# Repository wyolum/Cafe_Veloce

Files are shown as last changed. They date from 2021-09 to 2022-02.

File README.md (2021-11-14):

# Cafe_Veloce
Controller board for eBicycle lighting
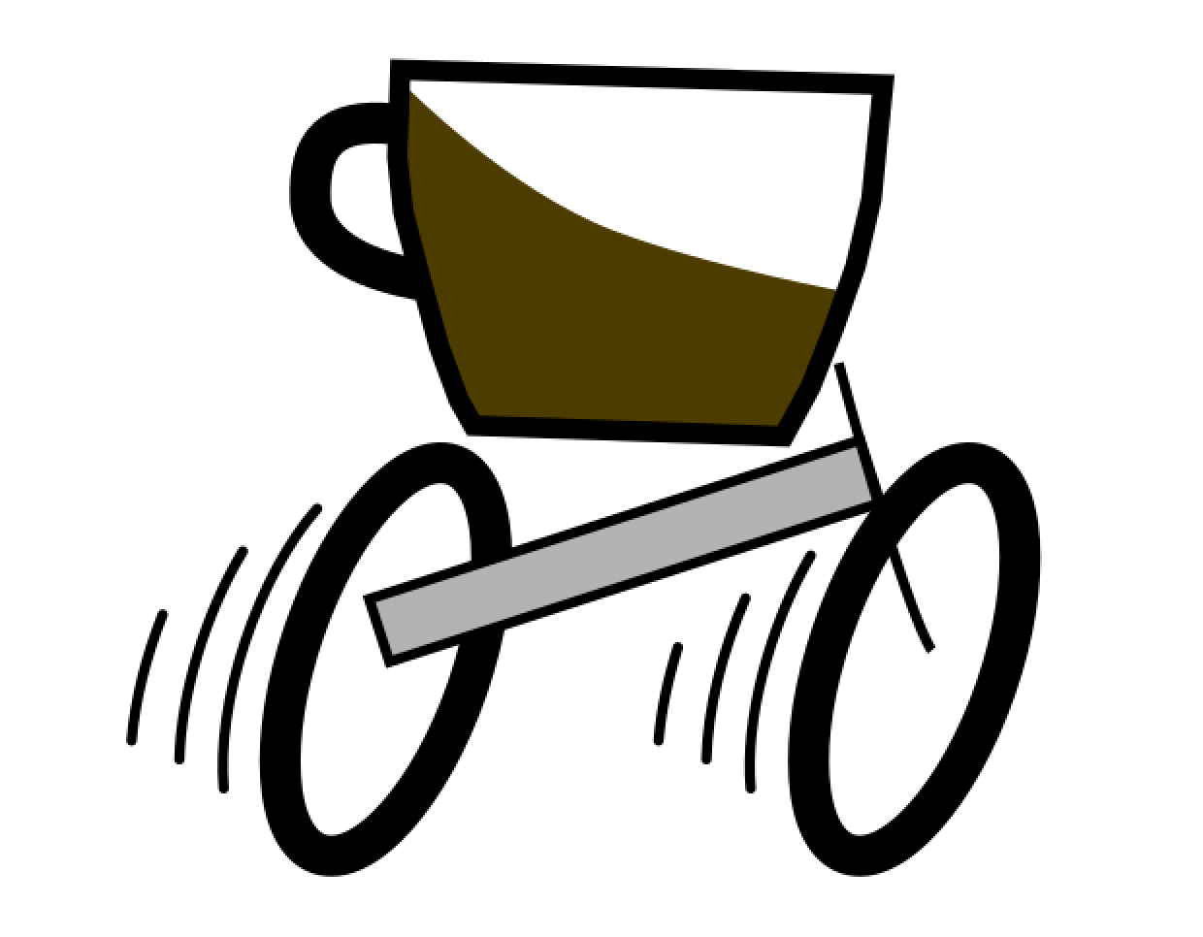
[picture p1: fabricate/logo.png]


**Renders**
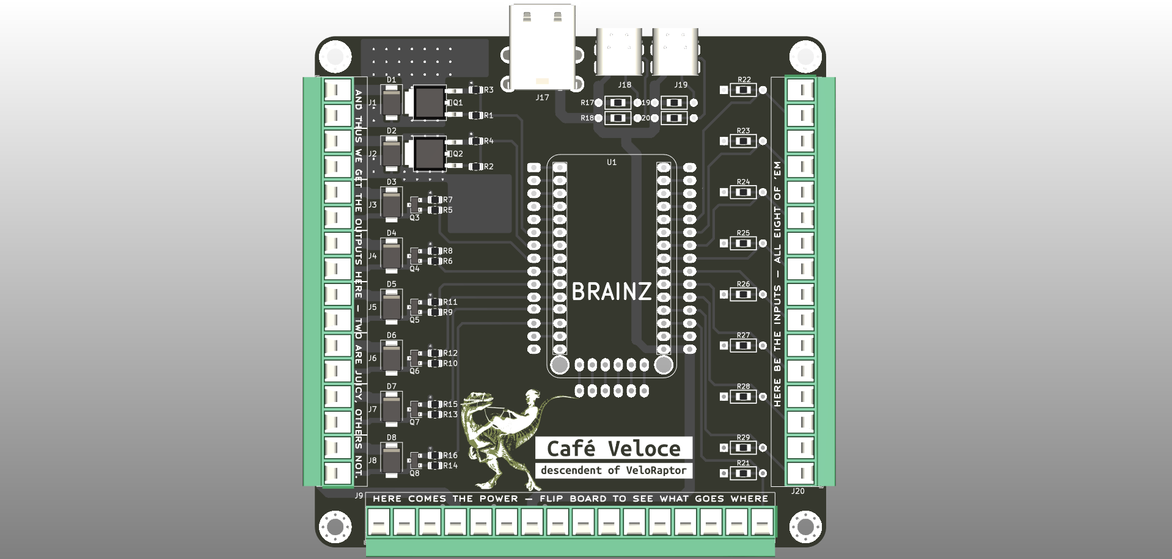
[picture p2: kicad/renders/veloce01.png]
Cafe Veloce


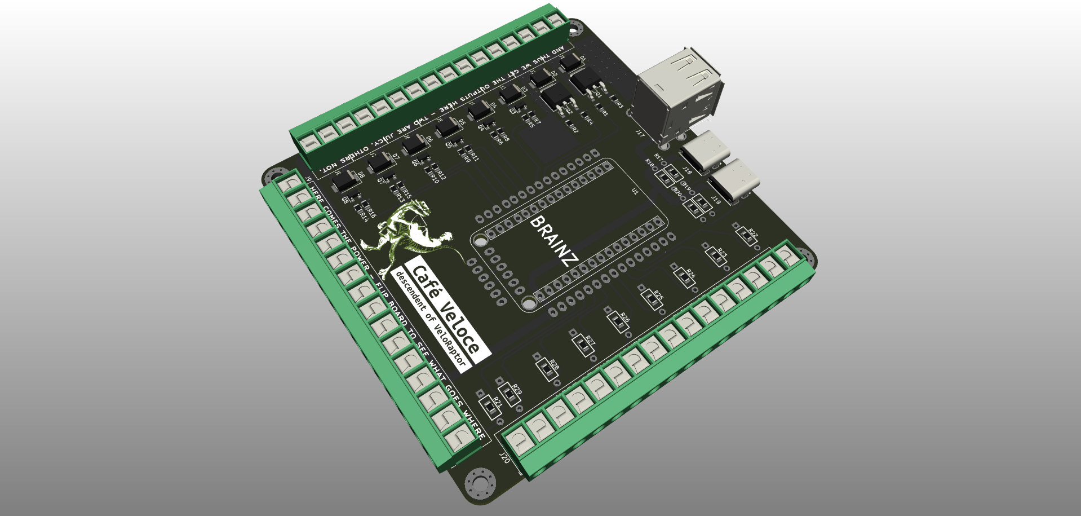
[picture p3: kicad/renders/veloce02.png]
Cafe Veloce


License
-------
[CERN Open Hardware Licence v1.2 ]

[CERN Open Hardware Licence v1.2 ]:http://www.ohwr.org/attachments/2388/cern_ohl_v_1_2.txt

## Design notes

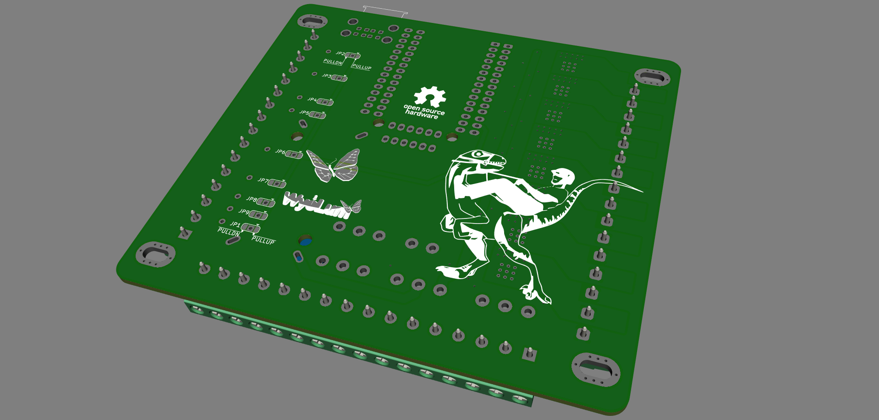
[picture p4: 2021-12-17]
kicad_v2/renders/veloce04.png

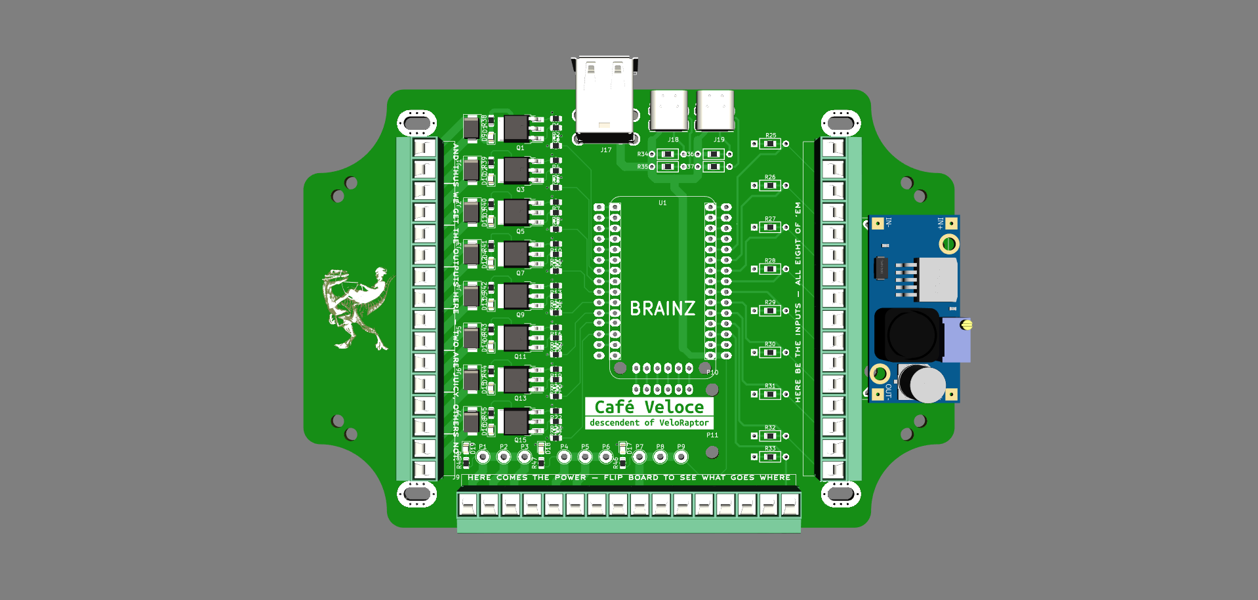
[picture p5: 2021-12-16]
kicad_v2/renders/veloce08.png

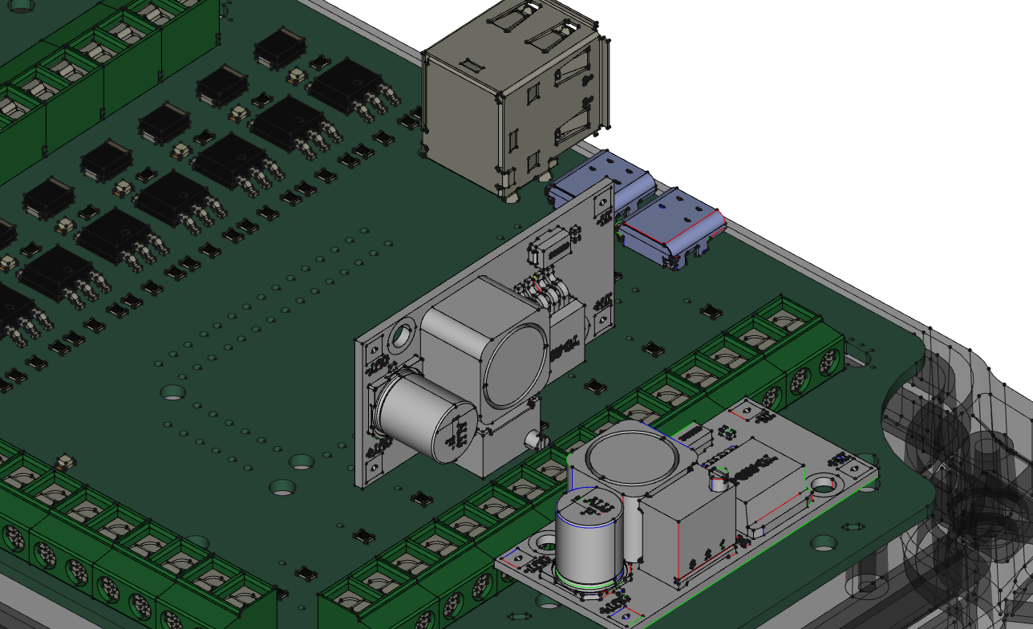
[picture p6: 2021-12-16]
CAD/renders/cafe_veloce_09.png

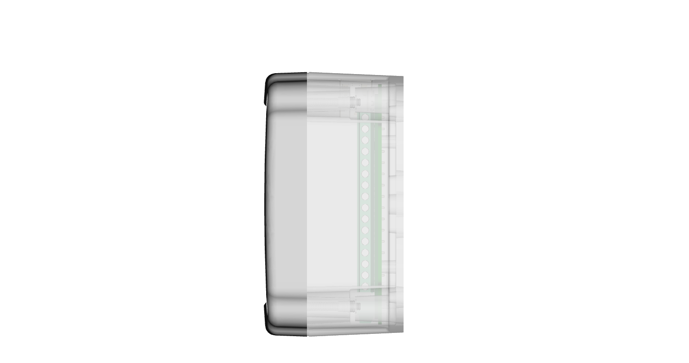
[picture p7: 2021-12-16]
CAD/renders/cafe_veloce_02.png

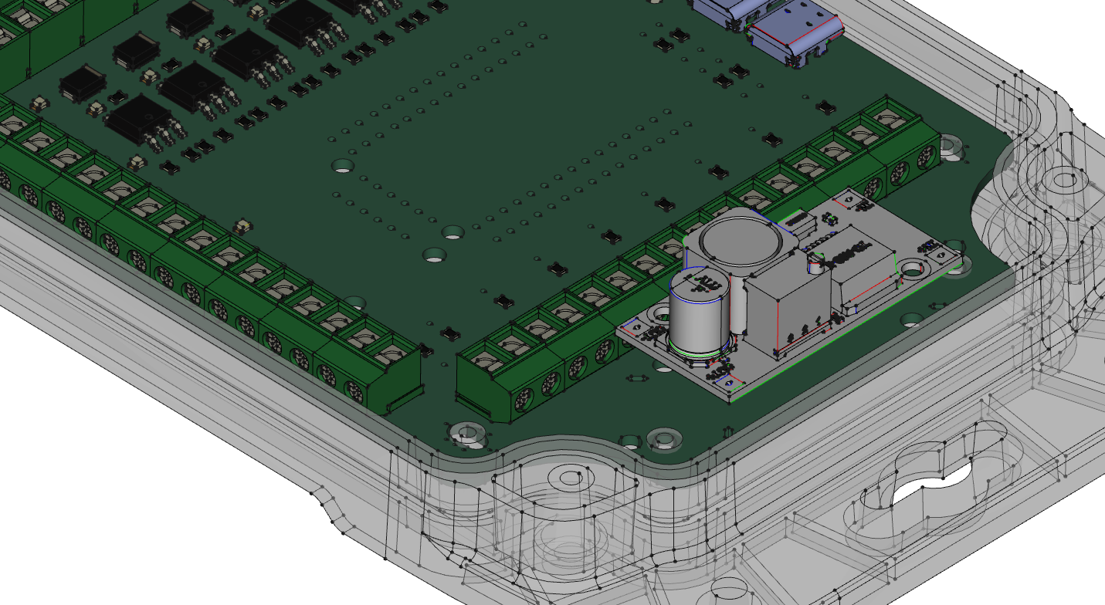
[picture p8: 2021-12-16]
CAD/renders/cafe_veloce_06.png

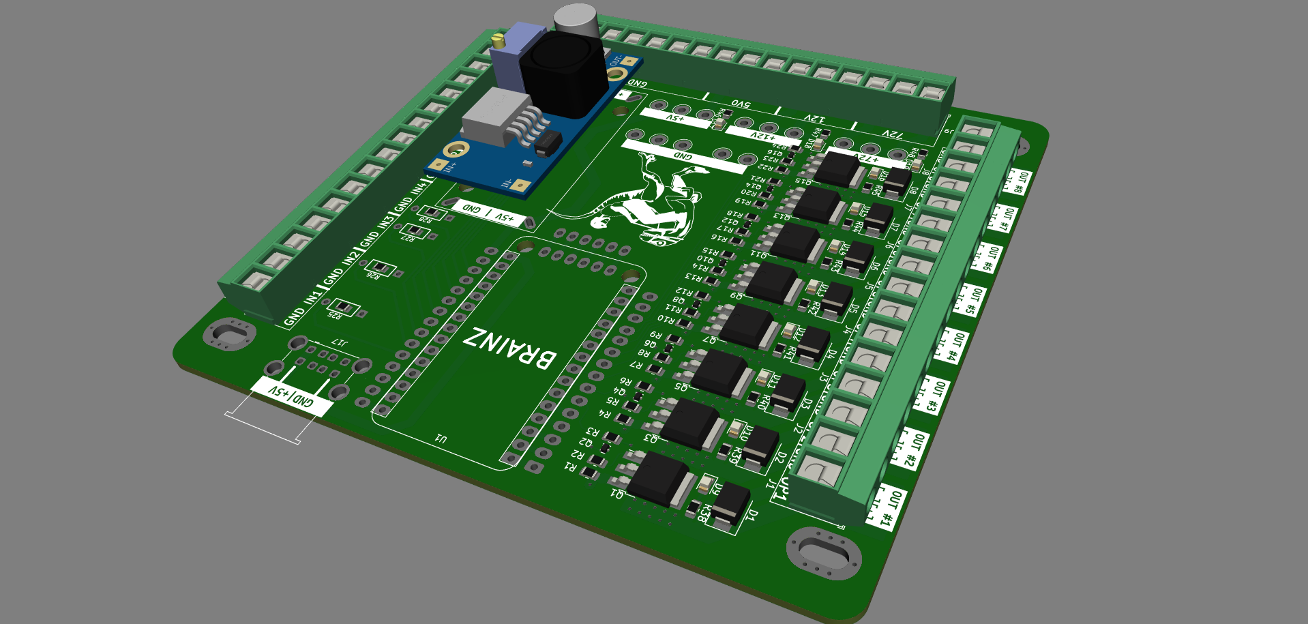
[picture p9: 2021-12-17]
kicad_v2/renders/veloce03.png

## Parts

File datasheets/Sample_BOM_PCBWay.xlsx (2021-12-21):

 |  |  | xxxx xxxx xxxxx xxPCS BOM (Sample Bill of Materials)
Item # | *Designator | *Qty | Manufacturer | *Mfg Part # | Description / Value | *Package/Footprint | Type | Your Instructions / Notes
1 | U1 | 1 | Linear | LTC3780EG#PBF | IC BUCK-BOOST CONV 24-SSOP | 24-SSOP | SMD
2 | U2,U4 | 2 | Fairchild | LM2904M | IC OPAMP DUAL -40-85 C 8-SOIC | 8-SOIC | DNS
3 | U3 | 1 | ON | LM317MBDTG | LM317M IC REG VOLT ADJ 500MA DPAK | DPAK | SMD
4 | U5 | 1 | Microchip | PIC16F690-I/SS | IC PIC MCU FLASH 4KX14 20SSOP | 20SSOP | SMD
5 | Q1 | 1 | Diodes Inc | GBJ10005-F | RECT BRIDGE GPP 50V 10A GBJ | GBJ | SMD
6 | R14,R18 | 2 | Panasonic | ERJ-6ENF4701V | RES 4.70K OHM 1/8W 1% 0805 SMD | 0805 | SMD
7 | R15 | 1 | Susumu | RL3720WT-R022-F | RES .022 OHM 1W 1% 0815 SMD | 0815 | SMD
8 | R16, R31 | 2 | Panasonic | ERJ-6ENF4702V | RES 47.0K OHM 1/8W 1% 0805 SMD | 0805 | SMD
9 | C5 | 1 | Murata | GRM21BR71C225KA12L | CAP CER 2.2UF 16V X7R 0805 | 0805 | SMD
10 | C7 | 1 | Murata | GRM21BR71C475KA73L | CAP CER 4.7UF 16V X7R 0805 | 0805 | DNS
11 | C8,C22 | 2 | Muruta | GRM21BR71C105KA01L | CAP CER 1.0UF 16V 10% X7R 0805 | 0805 | SMD
12 | CN6 | 1 | Molex | 538-53398-0671 | 1.25mm Connectors VERTICAL HDR SMT 6P | SMT 6P | SMD
13 | L1,L2 | 2 | Coiltronics | DR127-150-R | INDUCTOR SHIELD PWR 15UH SMD | SMD | SMD
14 | L3 | 1 | TDK | ACM1211-102-2PL-TL | CHOKE COMM MODE 1000 OHM 6A SM | SMD | SMD
15 | CN3,CN4 | 2 | Molex | 53047-0510 | CONN HEADER 5POS 1.25MM VERT TIN | 5POS | thru-hole
Need a quick and accurante quote? Need an efficient production? Please read SMT Ordering Necessary Files & Info in 1 minute. Thank you very much! (https://www.pcbway.com/smt_ordering_guide.html)
Click for Instructions on How to Create a BOM (https://www.pcbway.com/blog/PCB_Assembly/How_to_Build_a_BOM__Bill_Of_Materials_.html)

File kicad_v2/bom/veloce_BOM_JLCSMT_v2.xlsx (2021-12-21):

Comment | Designator | Footprint | JLCPCB Part #（optional）
B220A-13-F | D8,D7,D6,D5,D4,D3,D2,D1 | D_SMA | C110481
LED | D19,D18,D17,D16,D15,D14,D13,D12,D11,D10,D9 | LED_0805_2012Metric | C397047
FQD11P06TM | Q3,Q1 | TO-252-3_TabPin2
ZXMP7A17K | Q15,Q13,Q11,Q9,Q7,Q5 | TO-252-3_TabPin2
RUM001L02T2CL | Q16,Q14,Q12,Q10,Q8,Q6,Q4,Q2 | SOT-723 | C253528
0E | R23,R20,R17,R14,R11,R8,R5,R2 | R_0805_2012Metric | C25275
12k | R24,R22,R21,R19,R18,R16,R15,R13,R12,R10,R9,R7,R6,R4,R3,R1 | R_0805_2012Metric | C25616
10k | R32,R31,R30,R29,R28,R27,R26,R25,R33 | r_0805_THT | C25612
1k | R45,R44,R43,R42,R41,R40,R39,R38 | R_0805_2012Metric | C25623
510E | R46 | R_0805_2012Metric | C25317
1k8 | R47 | R_0805_2012Metric | C26016
5k6 | R48 | R_0805_2012Metric | C26024

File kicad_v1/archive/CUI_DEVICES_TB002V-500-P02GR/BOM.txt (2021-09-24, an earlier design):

3DX_CUI_DEVICES_Supplier: CUI Devices
3DX_CUI_DEVICES_Part Number: TB002V-500-P02GR
3DX_CUI_DEVICES_Description: 2~24 Poles, Screw Type, Vertical, 5.0 Pitch, 22-12 (AWG), Terminal Block Connector

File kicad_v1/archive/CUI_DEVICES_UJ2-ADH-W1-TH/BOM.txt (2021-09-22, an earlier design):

3DX_CUI_DEVICES_Supplier: CUI Devices
3DX_CUI_DEVICES_Description: 3 µin Plating Thickness, White Insulator, USB Receptacle
3DX_CUI_DEVICES_Model Number: UJ2-ADH-W1-TH

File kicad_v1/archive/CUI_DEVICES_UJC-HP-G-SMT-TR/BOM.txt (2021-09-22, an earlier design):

3DX_CUI_DEVICES_Supplier: CUI Devices
3DX_CUI_DEVICES_Description: Type C, 5 A, Right Angle, Surface Mount (SMT), Power-Only USB Receptacle
3DX_CUI_DEVICES_Model Number: UJC-HP-G-SMT-TR

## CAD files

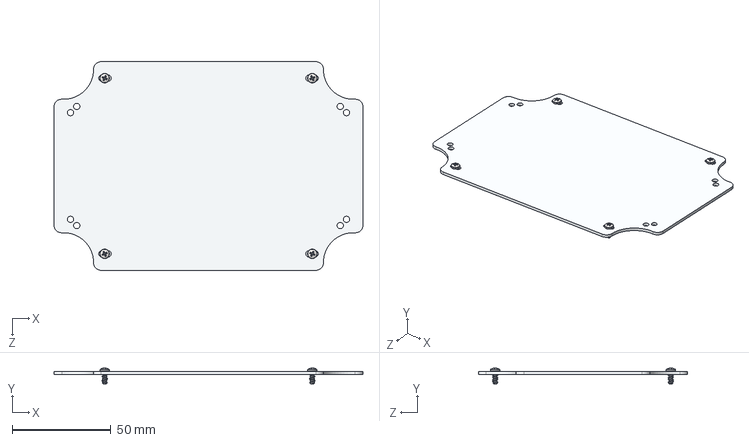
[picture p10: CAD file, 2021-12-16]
CAD/HD-45K-01_STEP/HD-45K-01.STEP
156.4 x 7.99 x 105.6 mm
HD-45P-01_DEFAULT
SCREWS-MBR x 4

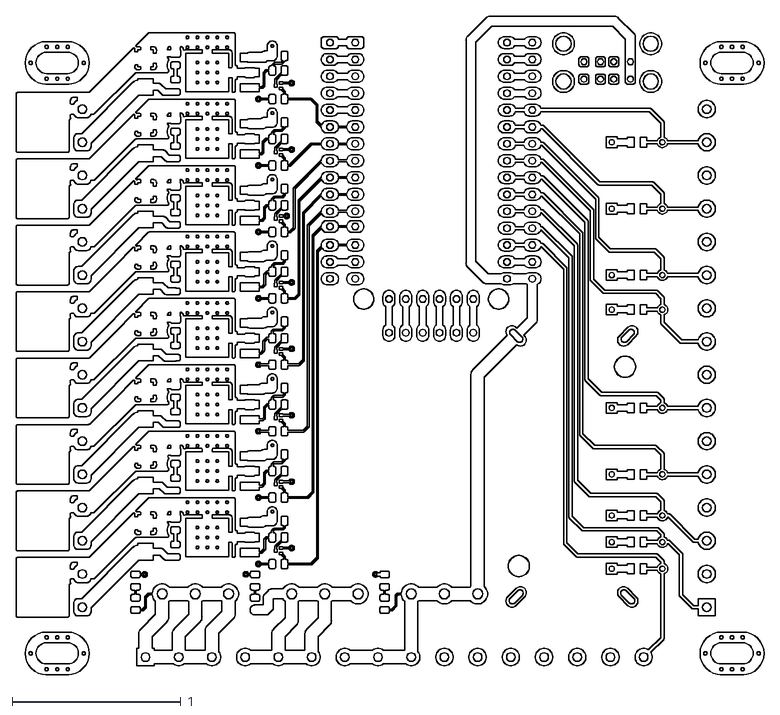
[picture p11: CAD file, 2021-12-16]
CAD/veloce-F_Cu.dxf
4.43 x 3.90

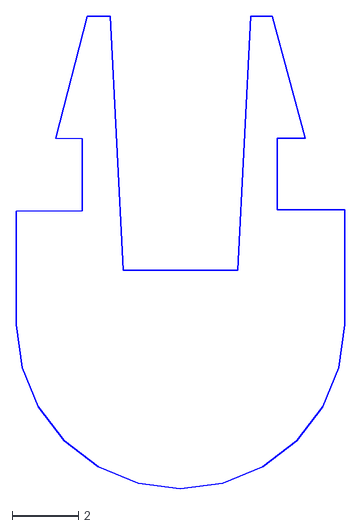
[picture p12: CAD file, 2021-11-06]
fabricate/cable_guide_0.dxf
9.90 x 14.3

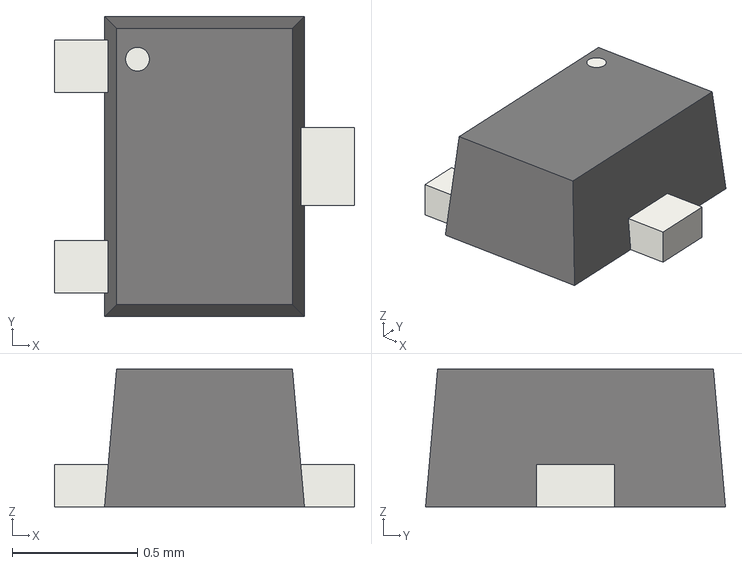
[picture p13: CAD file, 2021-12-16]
kicad_v2/3D_models/SOT_723.step
1.20 x 1.20 x 0.55 mm

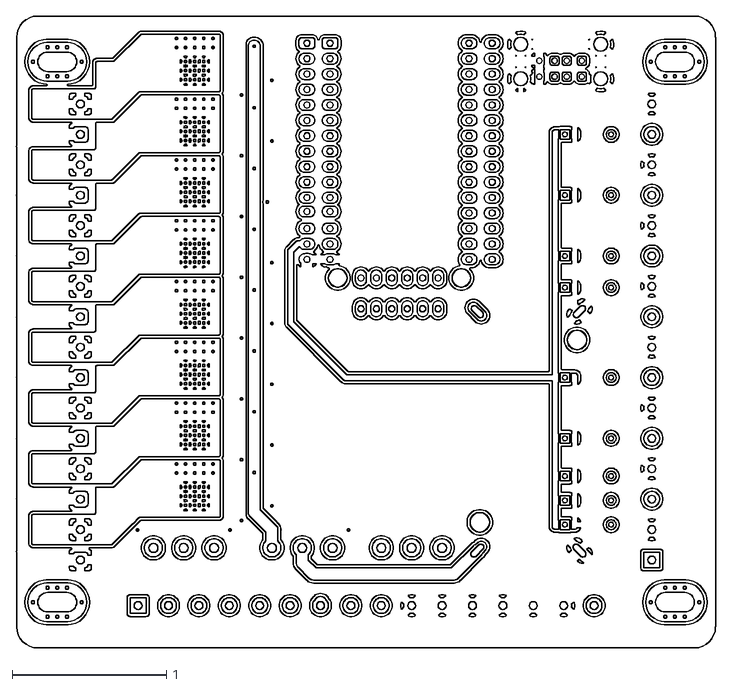
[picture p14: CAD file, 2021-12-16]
CAD/veloce-B_Cu.dxf
4.53 x 4.09

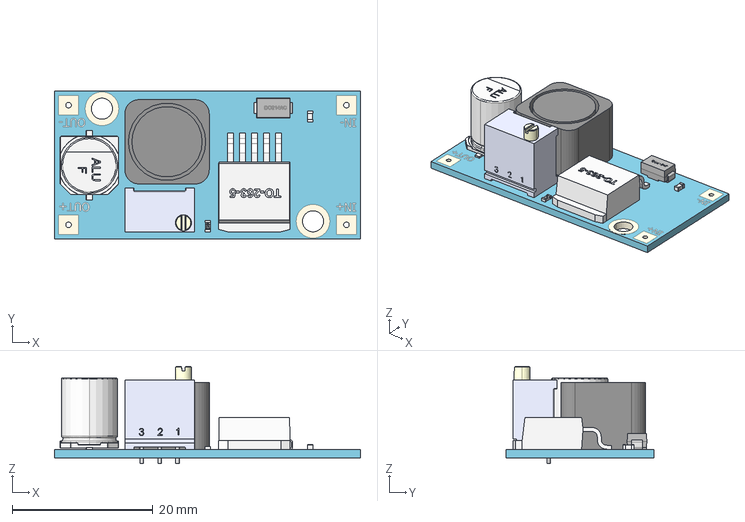
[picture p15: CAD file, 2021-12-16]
kicad_v2/3D_models/DC-DC_buck_LM2596s.step
43.5 x 21.0 x 13.8 mm

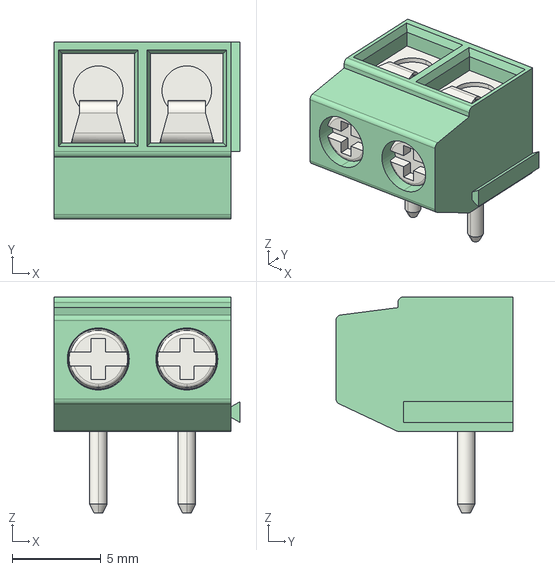
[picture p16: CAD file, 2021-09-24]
kicad_v2/3D_models/Conn_Wurth_RA_02.step
10.5 x 10.0 x 12.2 mm

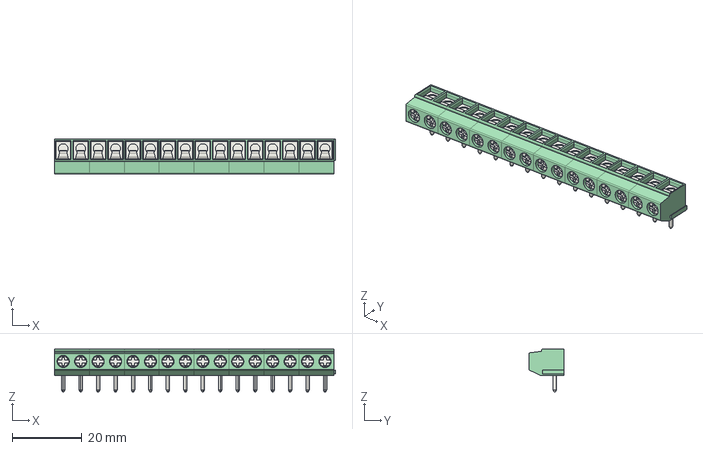
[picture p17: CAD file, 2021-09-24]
kicad_v2/3D_models/Conn_Wurth_RA_16.step
80.5 x 10.0 x 12.2 mm

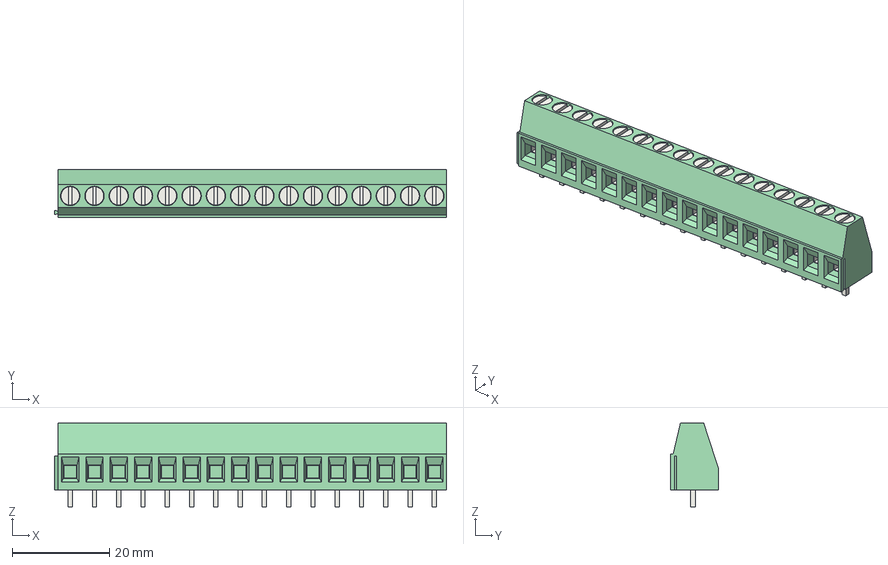
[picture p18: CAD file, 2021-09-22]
kicad_v2/3D_models/TerminalBlock_Phoenix_MKDS-1,5-16_1x16_P5.00mm_Horizontal.step
80.7 x 9.80 x 17.3 mm

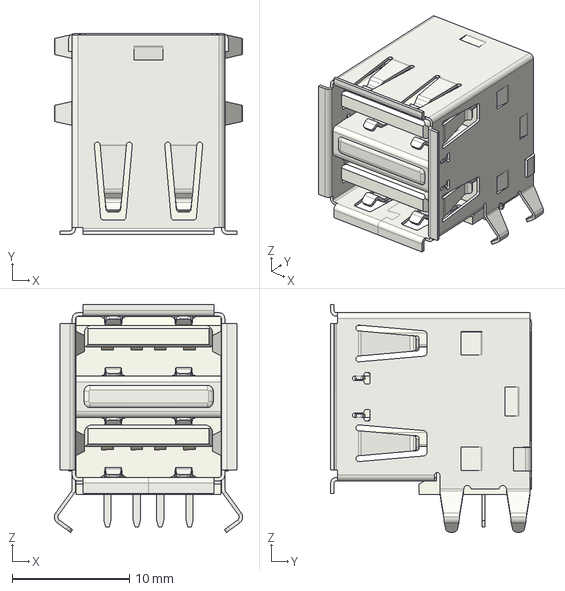
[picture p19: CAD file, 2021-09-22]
kicad_v2/3D_models/Conn_USB_A_stacked.step
16.0 x 17.1 x 19.4 mm

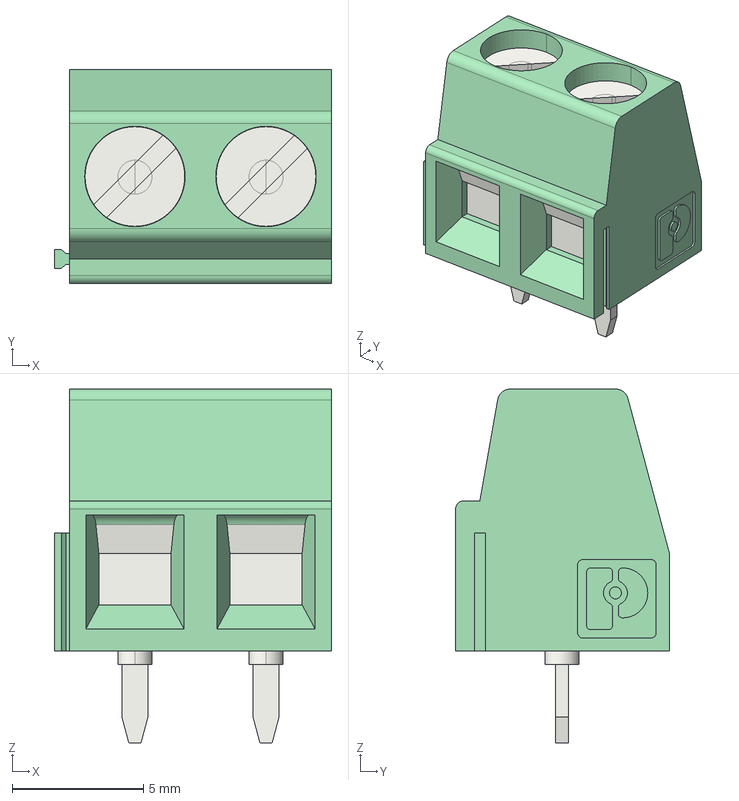
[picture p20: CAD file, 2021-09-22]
kicad_v2/3D_models/conn_wurth_691137710002.step
10.6 x 8.15 x 13.5 mm

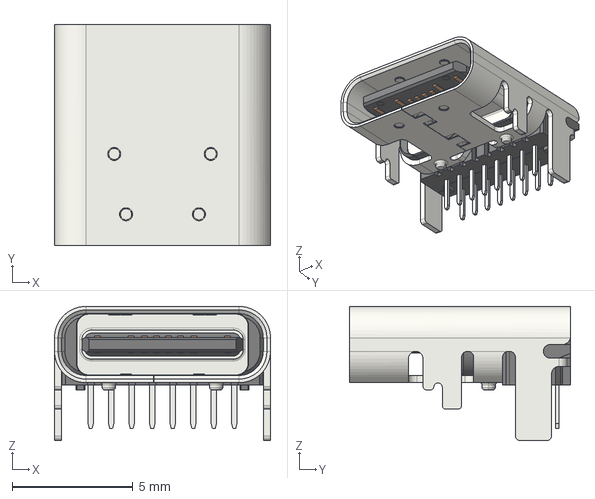
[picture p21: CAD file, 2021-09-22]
kicad_v2/3D_models/USB4085-GF-A.step
8.95 x 9.17 x 5.56 mm

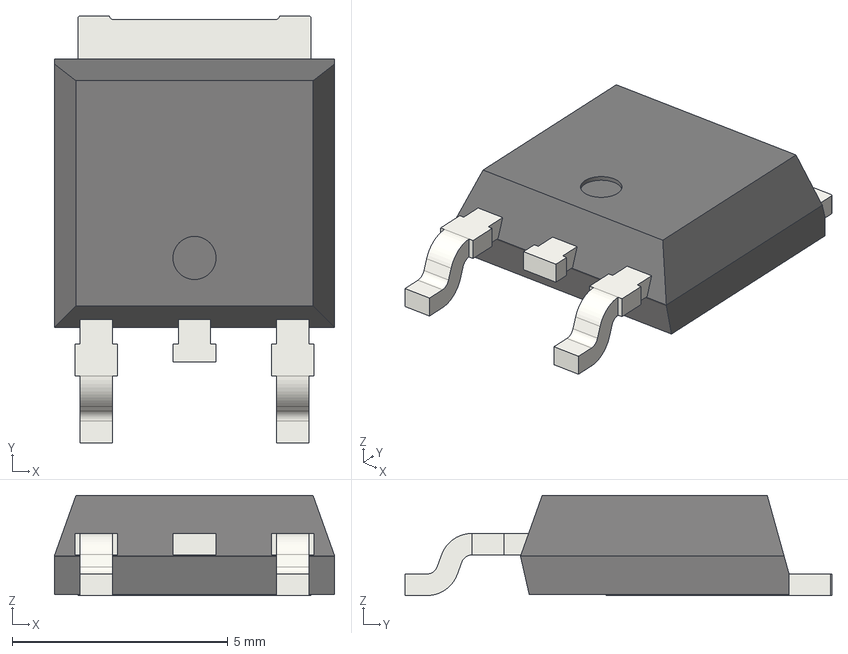
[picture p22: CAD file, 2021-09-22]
kicad_v2/3D_models/TO_252_2.step
6.50 x 9.90 x 2.32 mm

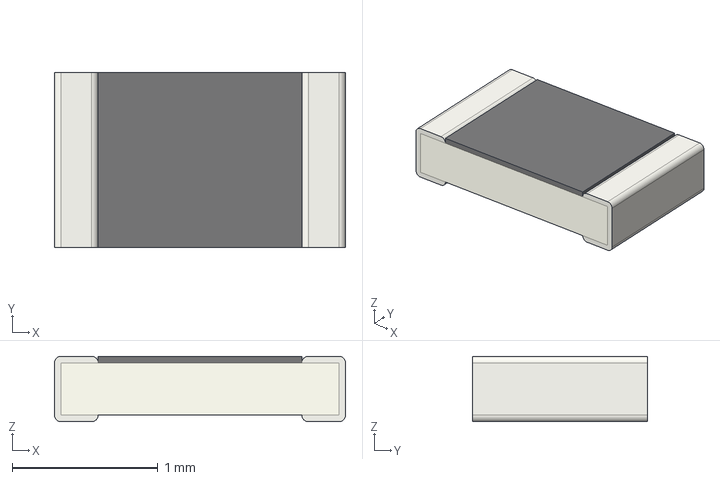
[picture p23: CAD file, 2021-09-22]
kicad_v2/3D_models/R_0805_2012Metric.step
2.00 x 1.20 x 0.45 mm

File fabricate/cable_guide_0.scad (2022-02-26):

$fn=50;
module guide(h, D){
difference(){
  color("grey")linear_extrude(height=h) import("cable_guide_0.dxf");
  translate([0, 0, -1])
    cylinder(h=h+2, d=D);
}
}
guide(15, 7.5);
//cylinder(h=11, d=6.7);
//cylinder(h=11, d=6.8);

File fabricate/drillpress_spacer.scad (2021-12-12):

$fn=50;
W = 14;
H = 7;
D = 8;

module washer(){
  difference(){
    cylinder(d=25.5, h=4);
    translate([0, 0, -1])cylinder(d=14.5, h=5);
  }
}

difference(){
  union(){
    translate([-W/2, -W/2, -3])cube([W, W, H + 3]);
  }
  translate([0, 0, -10])cylinder(h=100, d=D);
  translate([0, 0, -4])washer();
}
  

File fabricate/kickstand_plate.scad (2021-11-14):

/*
don't PLA will be strong enough.
*/

module p8020(len){
  difference(){
    cube([len, 80, 30]);
    translate([-1, 10 - 3, 0])cube([len + 2, 6, 6]);
    translate([-1, 30 - 3, 0])cube([len + 2, 6, 6]);
    translate([-1, 50 - 3, 0])cube([len + 2, 6, 6]);
    translate([-1, 70 - 3, 0])cube([len + 2, 6, 6]);
  }
}
module kick(){
  translate([0, -1, -18])
  difference(){
    cube([30, 80, 20]);
    translate([0, 15, -1])rotate([0, 0, 9])cube([40, 3, 100]);
    translate([-1, 65-3, -1])rotate([0, 0, -9])cube([40, 3, 100]);
    translate([2, -1, 0]) cube([3, 100, 100]);
    translate([25, -1, 0])cube([3, 100, 100]);
    translate([ 8, -1, 0])cube([2, 100, 100]);
    translate([20, -1, 0])cube([2, 100, 100]);
  }
}
//kick();

difference(){
  translate([0, 1, 0])cube([30, 78, 5]);
  translate([-1, 0, 3])p8020(102);
  kick();
  translate([15, 40, -1])cylinder(h=100, d=10, $fn=100);
}
/*
*/

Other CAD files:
CAD/cafe_veloce.FCStd
kicad_v2/3D_models/R_Axial_DIN0204_L36mm_D16mm_P762mm_Horizontal.step
kicad_v2/3D_models/TerminalBlock_Phoenix_MKDS-1,5-2_1x02_P5.00mm_Horizontal.step
kicad_v2/3D_models/SOT_23.step
kicad_v1/3D_models/D_SMB.step
kicad_v1/3D_models/R_Axial_DIN0204_L36mm_D16mm_P762mm_Horizontal.step
kicad_v1/3D_models/SOT_23.step
kicad_v1/3D_models/TerminalBlock_Phoenix_MKDS-1,5-2_1x02_P5.00mm_Horizontal.step
kicad_v1/3D_models/UJC-HP-G-SMT-TR.step
kicad_v1/3D_models/terminal_block_wurth_1377_16.step
kicad_v1/3D_models/terminal_block_wurth_1377_2.step
kicad_v1/archive/119926768-19-terminal_blocks_a-tb500-ti02/terminal_blocks_a-tb500-ti02.stp
kicad_v1/archive/CUI_DEVICES_TB002V-500-P02GR/CUI_DEVICES_TB002V-500-P02GR.step
kicad_v1/archive/CUI_DEVICES_TB002V-500-P16GR/CUI_DEVICES_TB002V-500-P16GR.step
kicad_v1/archive/CUI_DEVICES_UJ2-ADH-W1-TH/CUI_DEVICES_UJ2-ADH-W1-TH.step
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

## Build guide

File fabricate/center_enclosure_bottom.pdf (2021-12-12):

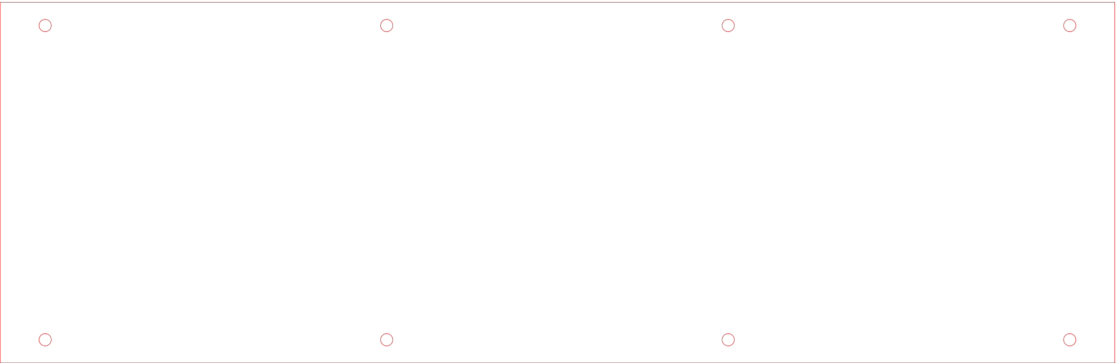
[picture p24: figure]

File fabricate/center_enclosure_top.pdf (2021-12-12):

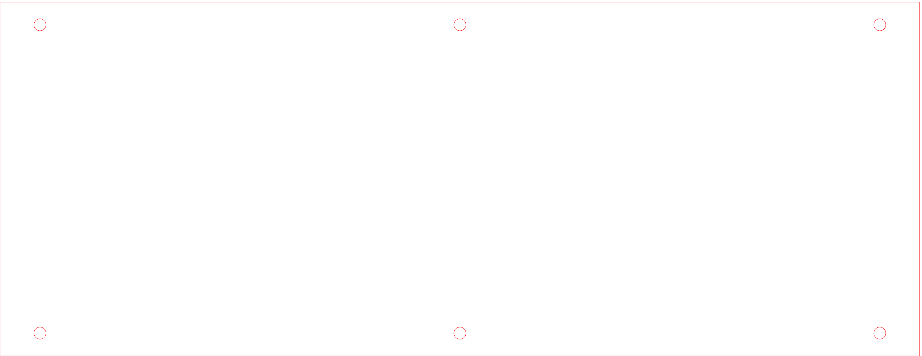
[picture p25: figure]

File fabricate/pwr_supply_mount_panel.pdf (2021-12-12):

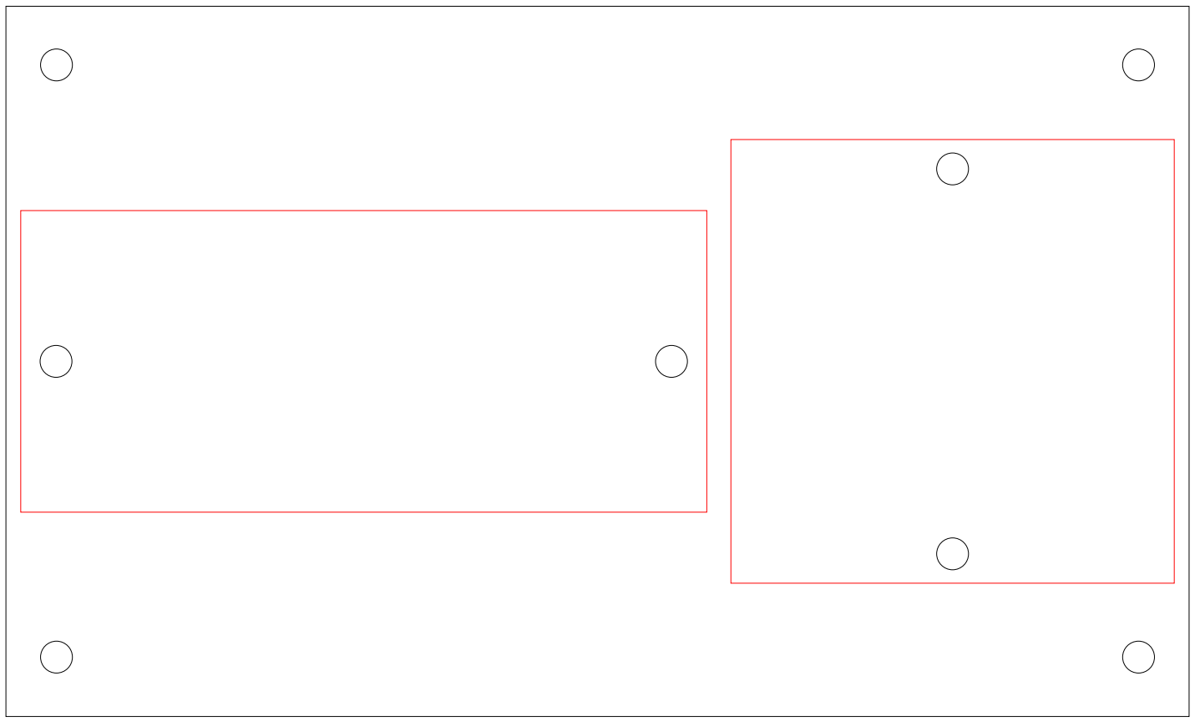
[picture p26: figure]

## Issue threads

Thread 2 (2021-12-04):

Topside labels

wyojustin, 2021-12-04:
Label input/output and voltage on the top side of the board.  once the board is attached, you can no longer see the labels.

Anool, 2021-12-16:
Done. Labels added to top side

Closed 2021-12-16.

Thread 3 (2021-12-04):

Add more voltage outputs for 5V and 12V

wyojustin, 2021-12-04:
There are no spare 12v outputs and only 1 spare 5V output.  Add a few more.

Anool, 2021-12-10:
Added and done

Closed 2021-12-10.

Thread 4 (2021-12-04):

Common ground on outputs.

wyojustin, 2021-12-04:
To be consistant with lighting packages, use common ground on outputs instead of common hot.

Anool, 2021-12-10:
Done. Outputs are high side switches now.

Closed 2021-12-10.

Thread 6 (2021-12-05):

Put 5v reg on board

wyojustin, 2021-12-05:
To reduce wires.  Put the 5v regulator on the board.  Just needs enough current to drive logic.

Anool, 2021-12-16:
Added footprint for LM2596 adjustable buck regulator.
Solder pads are inclined at 45 deg to accommodate slight size variations in Amazon modules

Closed 2021-12-16.

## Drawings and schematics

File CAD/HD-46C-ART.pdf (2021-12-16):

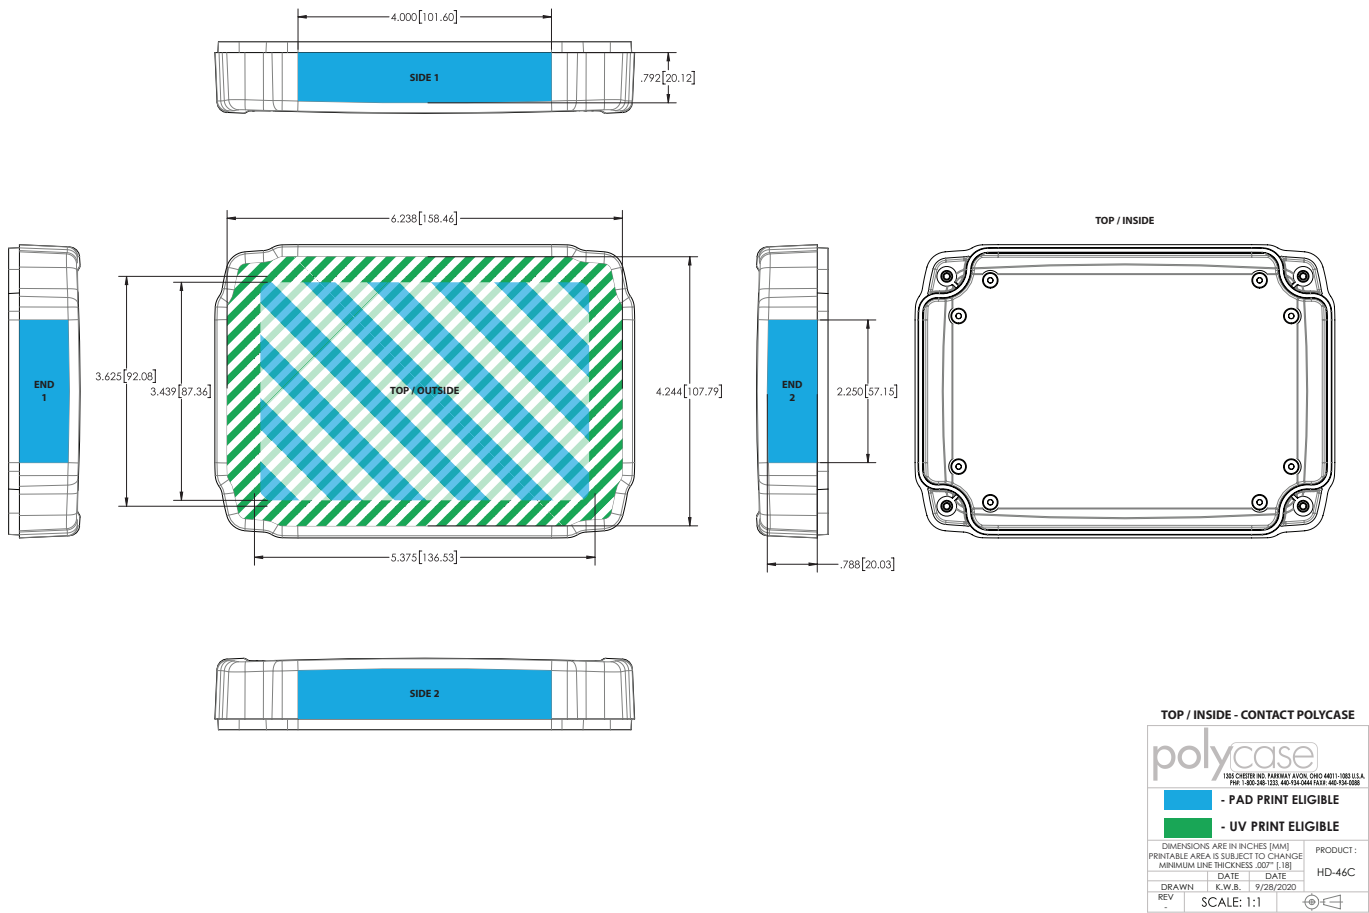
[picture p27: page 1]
TOP / INSIDE; TOP / OUTSIDE; SIDE 1; SIDE 2; END 2; END 1

TOP / INSIDE - CONTACT POLYCASE

- PAD PRINT ELIGIBLE
- UV PRINT ELIGIBLE

DIMENSIONS ARE IN INCHES [MM] PRINTABLE AREA IS SUBJECT TO CHANGE MINIMUM LINE THICKNESS .007” [.18] | PRODUCT : HD-46C

DATE | DATE

DRAWN | K.W.B. | 9/28/2020
REV -

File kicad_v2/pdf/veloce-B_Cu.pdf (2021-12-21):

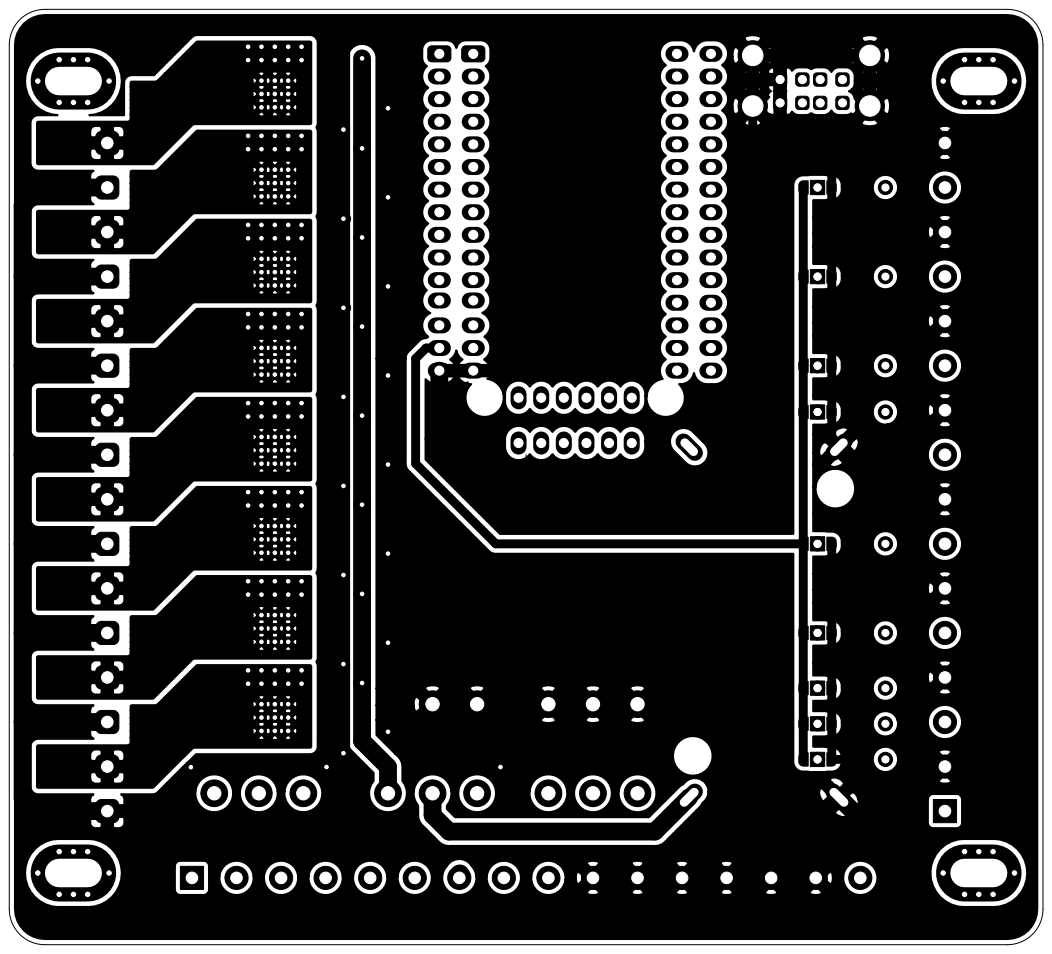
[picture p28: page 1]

File: veloce.kicad_pcb Sheet: Wyolum

Id: 1/1 Title: Cafe Veloce

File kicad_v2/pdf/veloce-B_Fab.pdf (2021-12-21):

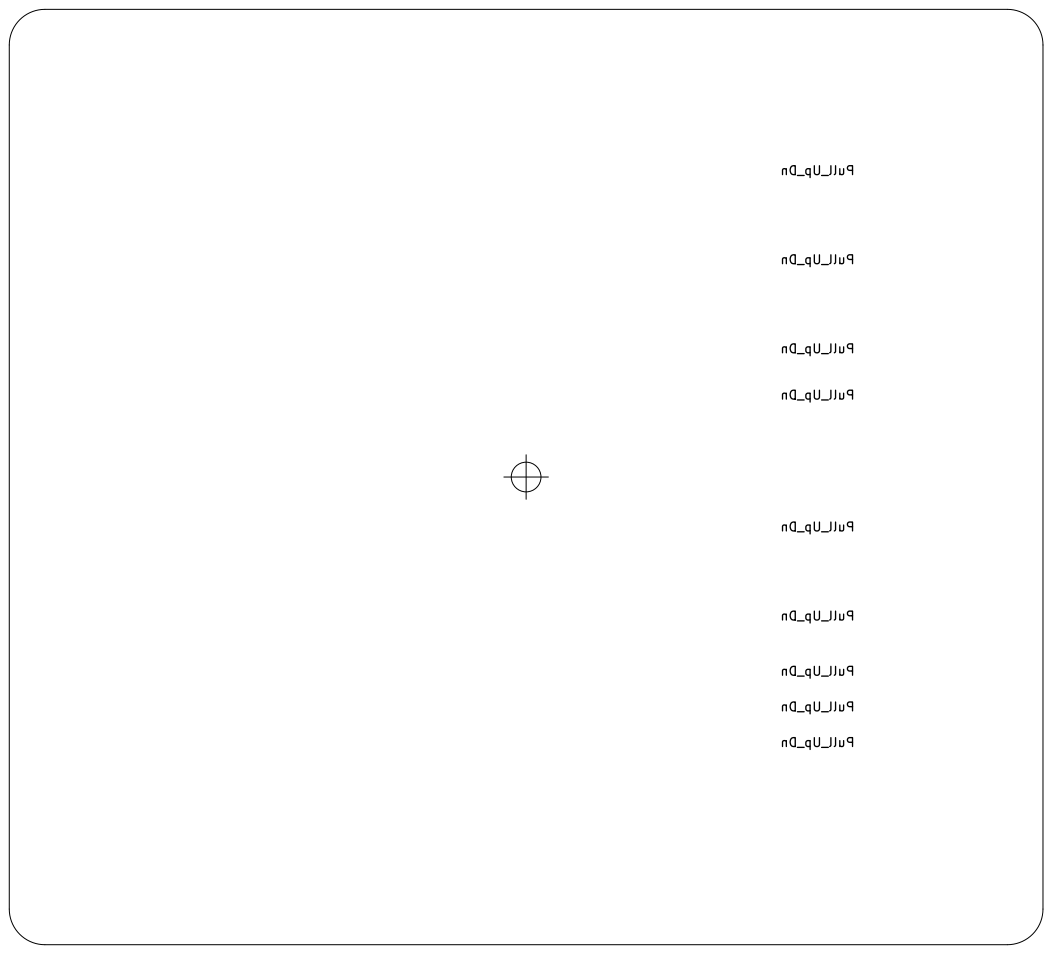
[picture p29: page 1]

File: veloce.kicad_pcb Sheet: Wyolum

Id: 1/1 Title: Cafe Veloce

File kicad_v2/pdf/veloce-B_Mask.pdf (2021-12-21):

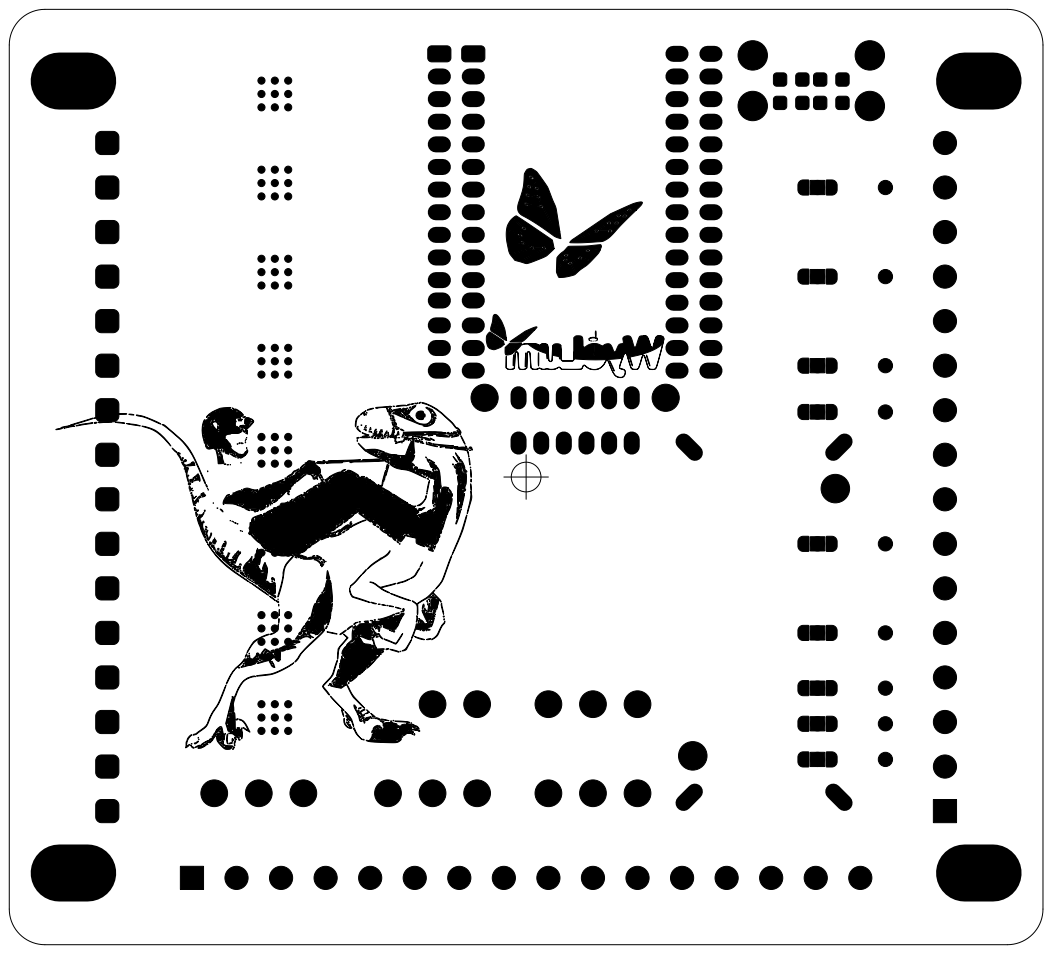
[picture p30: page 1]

File: veloce.kicad_pcb Sheet: Wyolum

Id: 1/1 Title: Cafe Veloce

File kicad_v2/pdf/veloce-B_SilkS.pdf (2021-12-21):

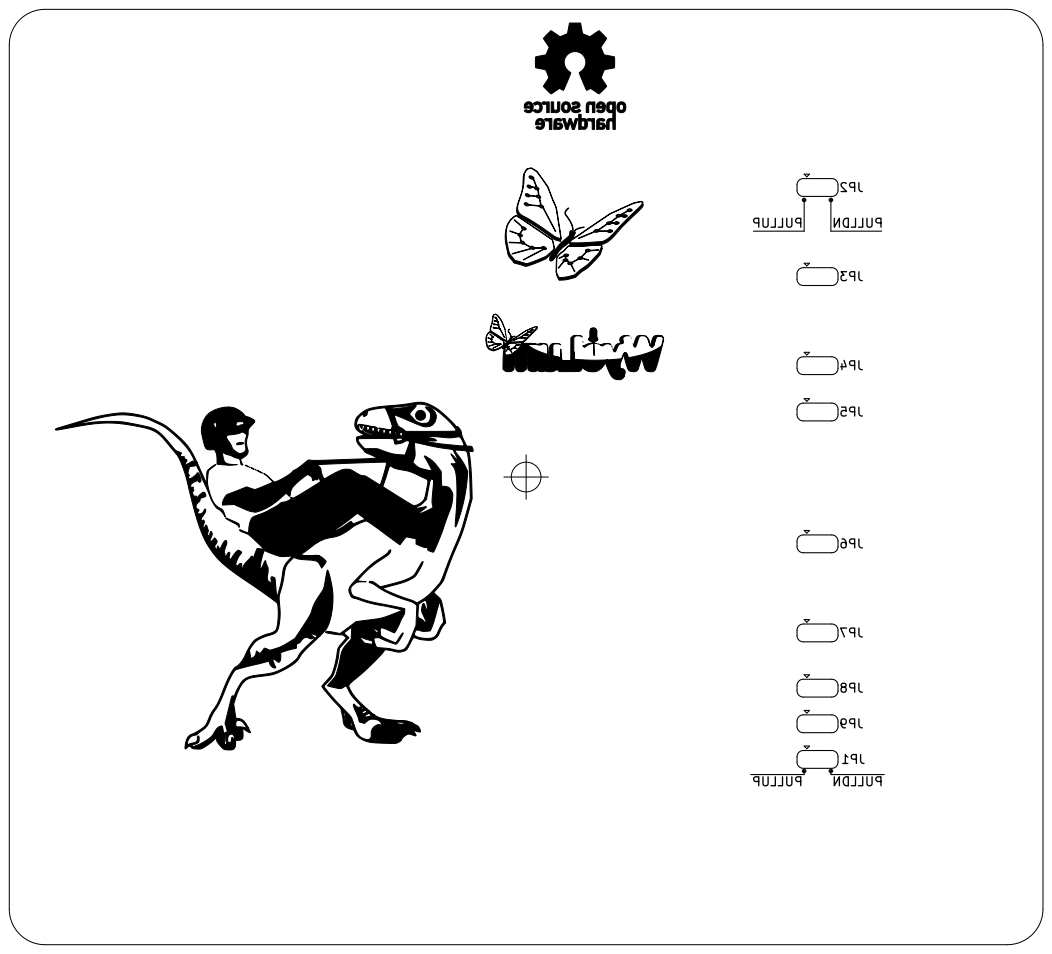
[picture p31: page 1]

File: veloce.kicad_pcb Sheet: Wyolum

Id: 1/1 Title: Cafe Veloce

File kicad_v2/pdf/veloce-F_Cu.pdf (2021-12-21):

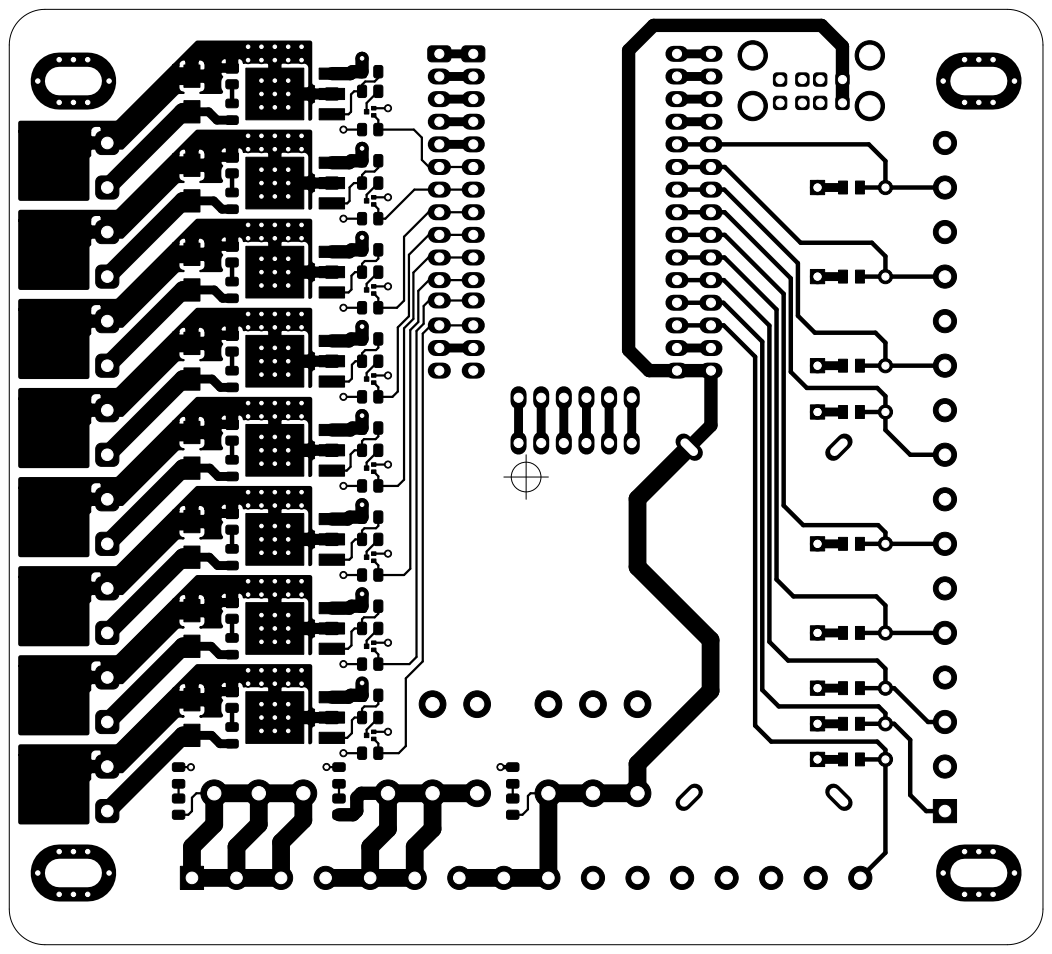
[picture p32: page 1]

File: veloce.kicad_pcb Sheet: Wyolum

Id: 1/1 Title: Cafe Veloce

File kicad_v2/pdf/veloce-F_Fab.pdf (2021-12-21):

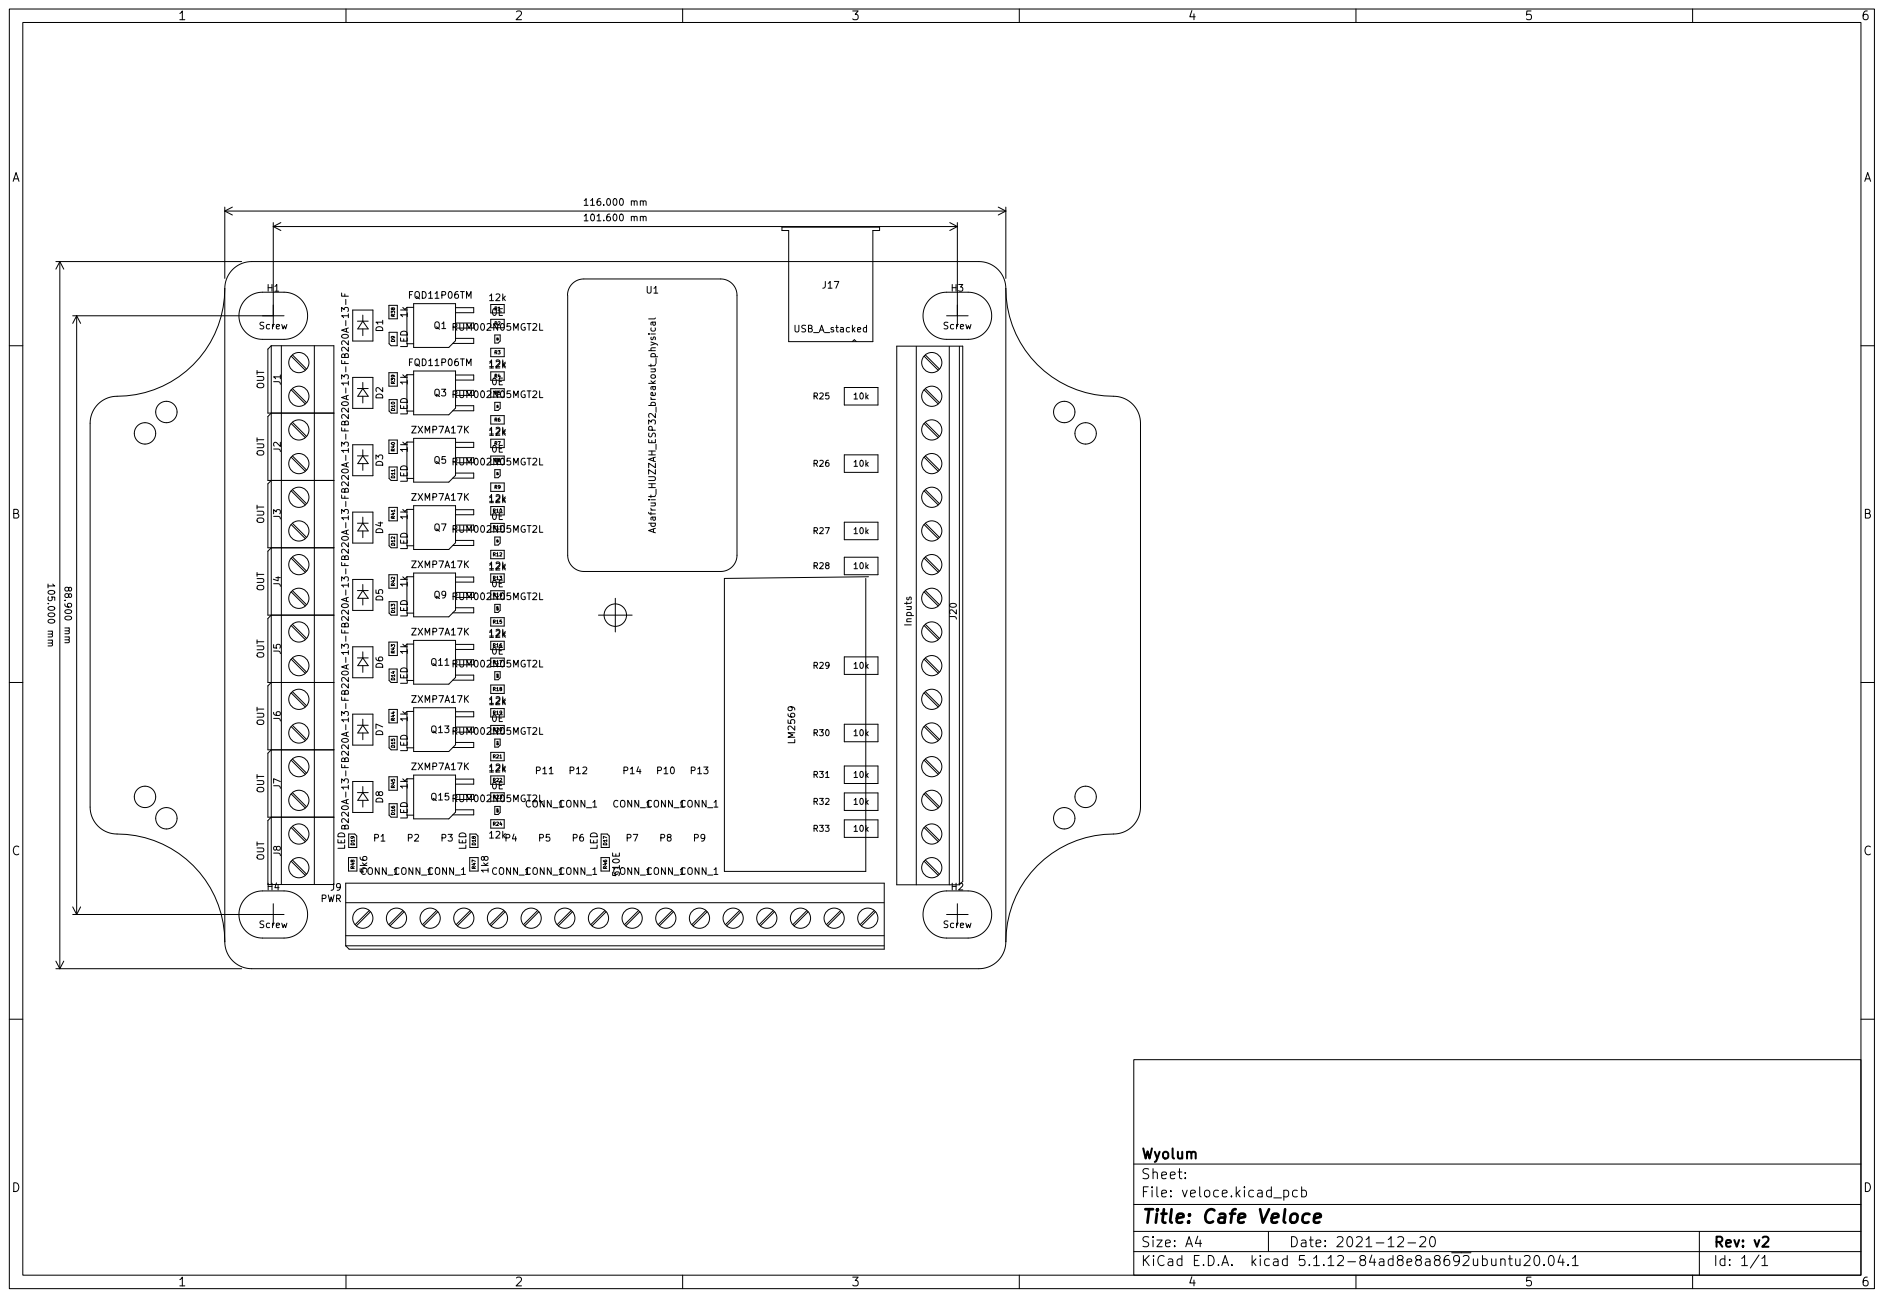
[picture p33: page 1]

USB_A_stacked

File: veloce.kicad_pcb Sheet: Wyolum 88.900 mm

Id: 1/1 Title: Cafe Veloce

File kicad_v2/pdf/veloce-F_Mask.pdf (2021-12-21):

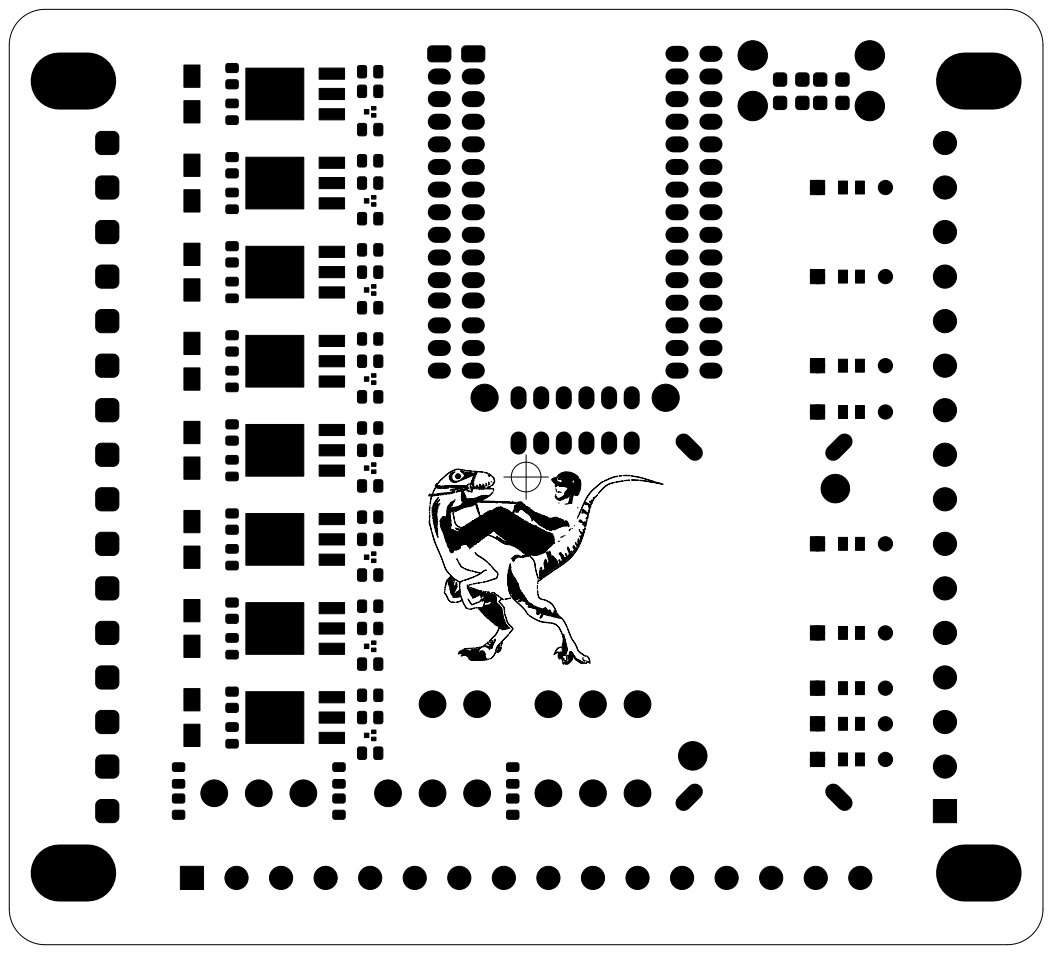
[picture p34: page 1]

File: veloce.kicad_pcb Sheet: Wyolum

Id: 1/1 Title: Cafe Veloce

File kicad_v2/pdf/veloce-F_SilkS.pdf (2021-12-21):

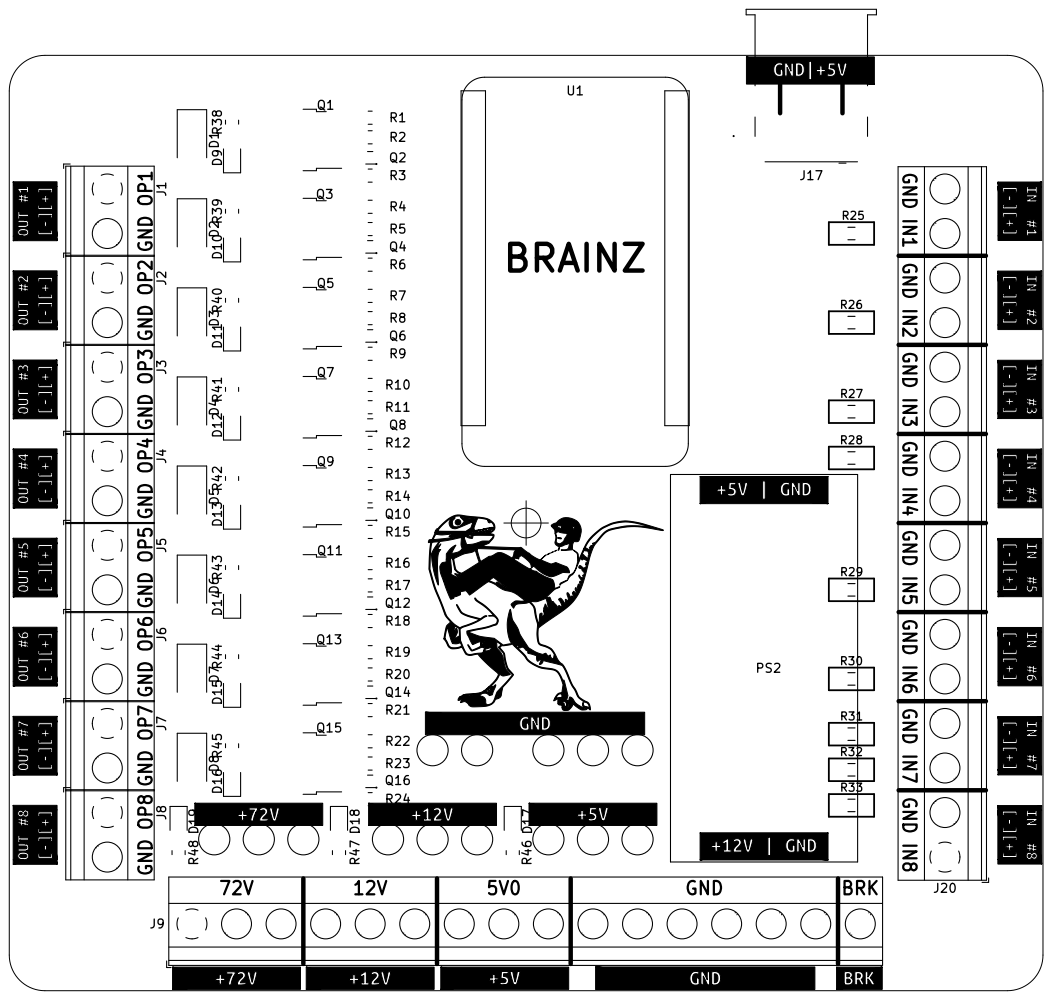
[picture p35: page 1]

File: veloce.kicad_pcb Sheet: Wyolum

Id: 1/1 Title: Cafe Veloce

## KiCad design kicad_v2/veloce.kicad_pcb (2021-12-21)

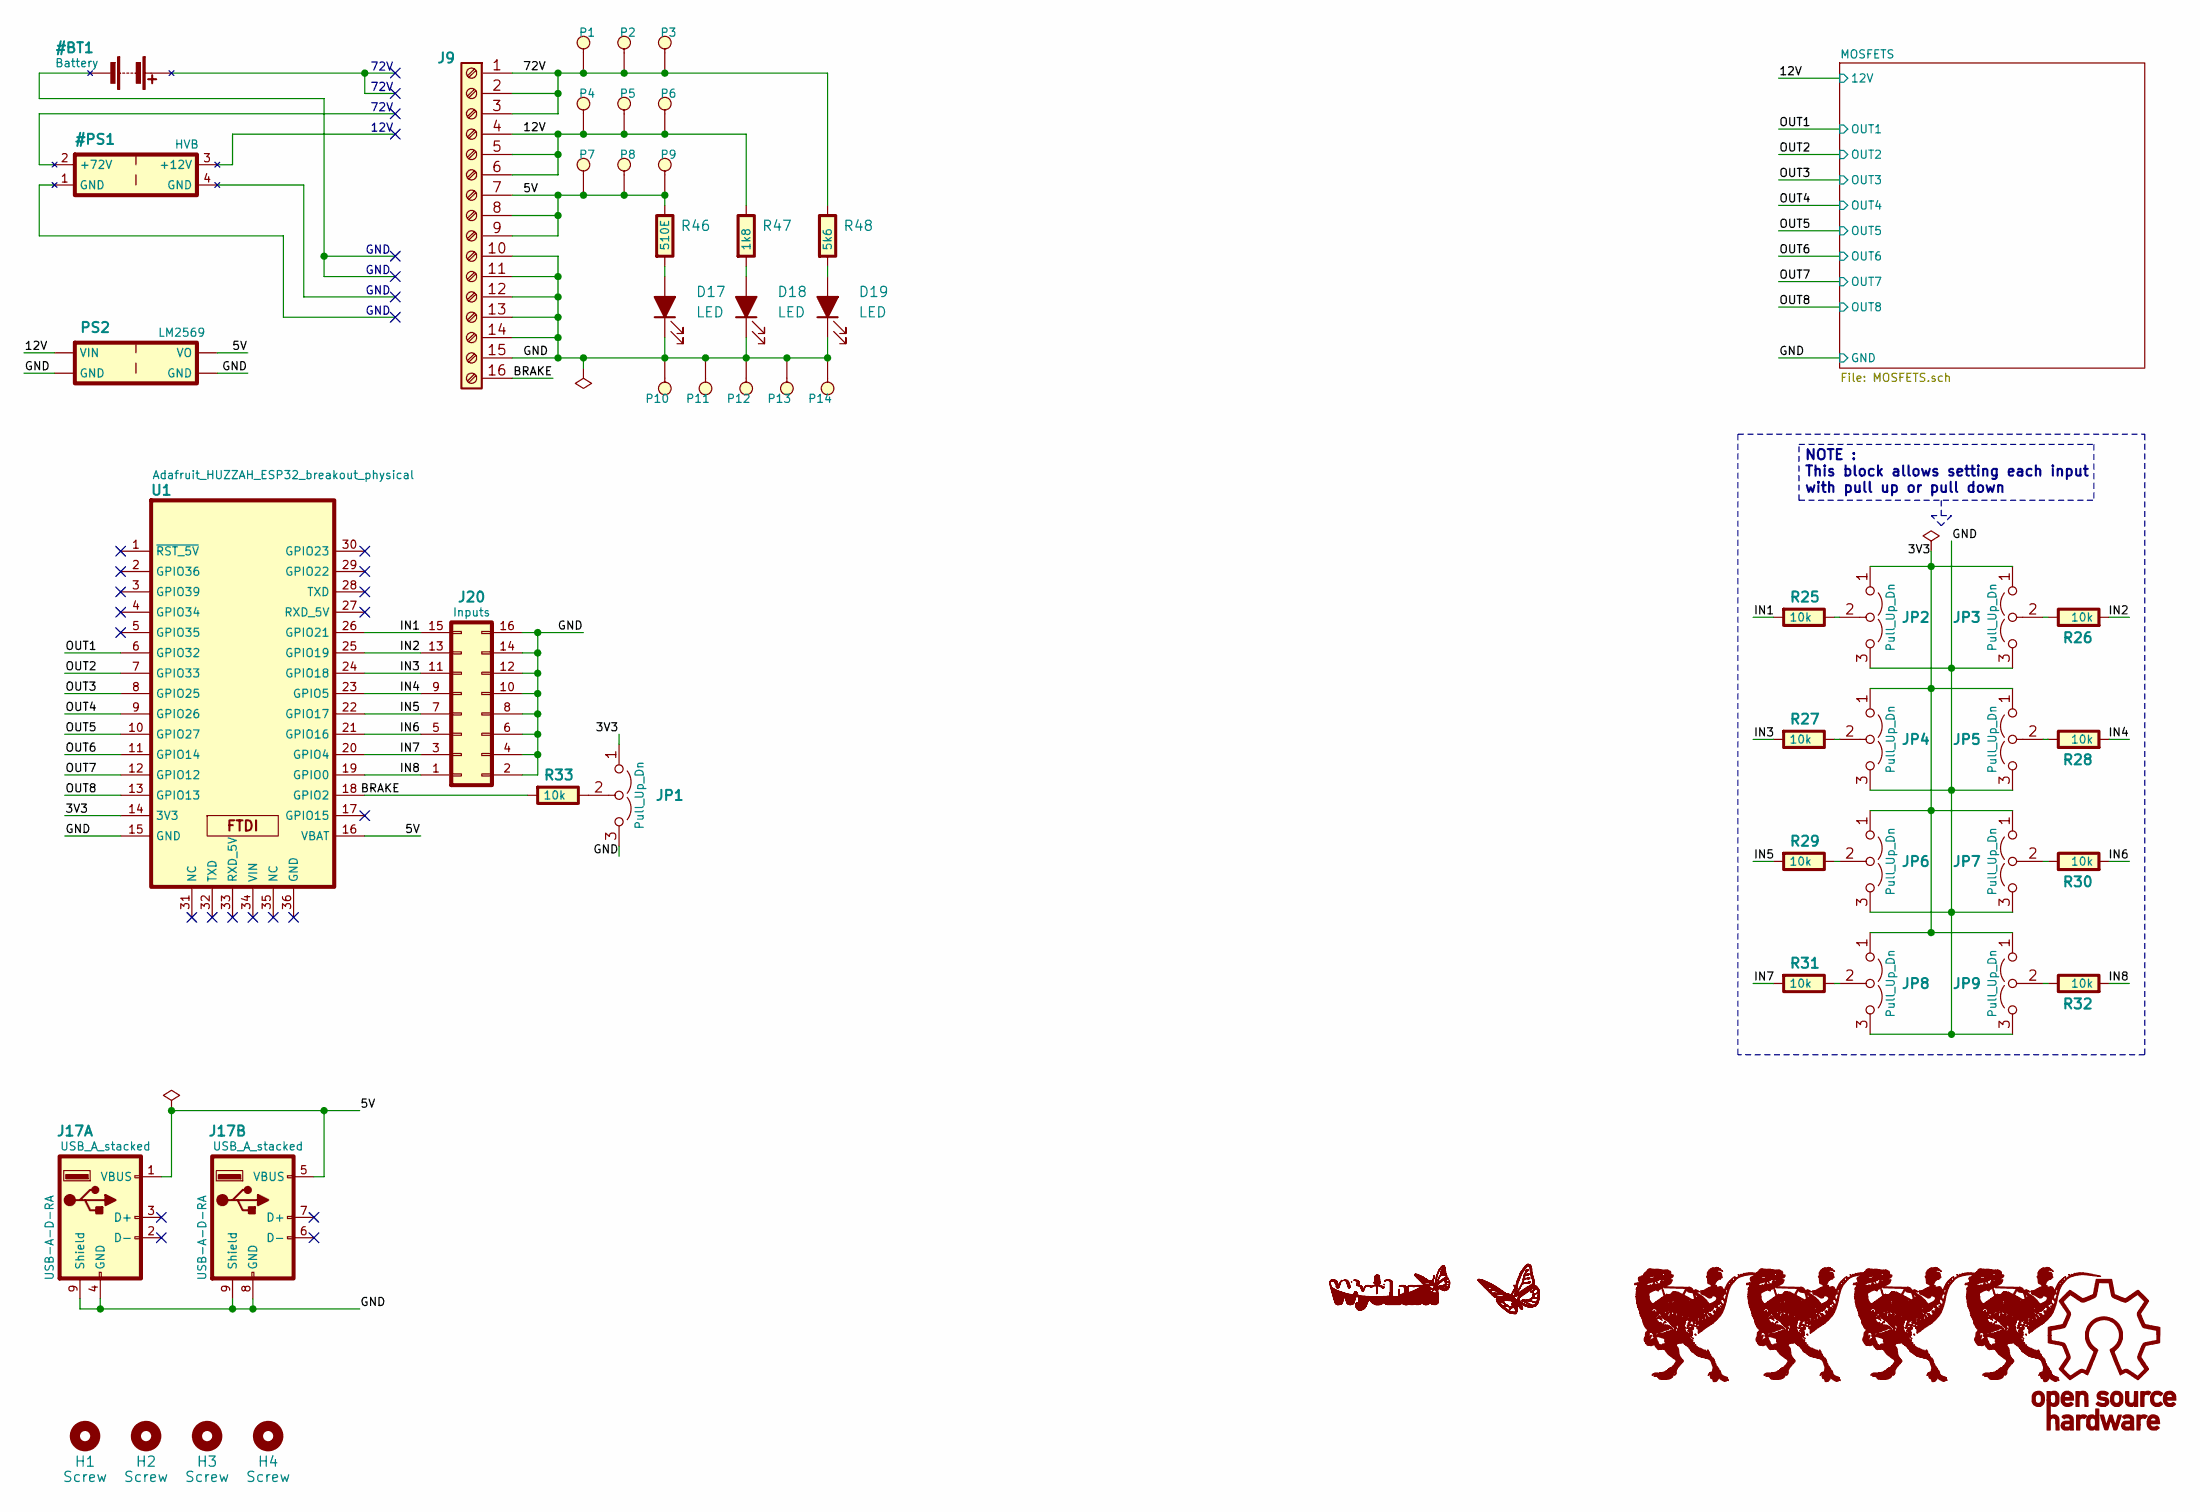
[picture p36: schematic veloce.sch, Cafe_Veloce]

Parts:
D17, D18, D19: LED; LED_0805_2012Metric
G1: Logo_Veloce; logo_CV_v2_silk
G2: Logo_Veloce; logo_VR_v2_mask
G3: Logo_Veloce; logo_CV_v2_silk2
G4: Logo_Veloce; logo_CV_v2_mask2
G5: LOGO_WL; logo_butterfly_silk_15x12
G6: LOGO_WL; logo_butterfly_mask_15x12
G7: Logo_OSHW; Logo_OSHW-11.4x12mm_SilkScreen
G8: Logo_Wyolum; logo_wyolum_silk_20x8
G9: Logo_Wyolum; logo_wyolum_mask_20x8
H1, H2, H3, H4: Screw; MountingHole_3.2mmx6.4mm_M3_Pad_Via
J9: PWR; TerminalBlock_Wurth_1377-16_Horizontal
J17: USB_A_stacked; USB_A_Wuerth_61400826021_Horizontal_Stacked
J20: Inputs; TerminalBlock_Wurth_1377-16_Horizontal
JP1, JP2, JP3, JP4, JP5, JP6, JP7, JP8, JP9: Pull_Up_Dn; SolderJumper-3_P1.3mm_Open_RoundedPad1.0x1.5mm_THT
P1, P2, P3, P4, P5, P6, P7, P8, P9, P10, P11, P12, P13, P14: CONN_1; TestPoint_THTPad_D3.0mm_Drill1.5mm
PS2: LM2569; 5VReg_module_LM2596
R25, R26, R27, R28, R29, R30, R31, R32, R33: 10k; r_0805_THT
R46: 510E; R_0805_2012Metric
R47: 1k8; R_0805_2012Metric
R48: 5k6; R_0805_2012Metric
U1: Adafruit_HUZZAH_ESP32_breakout_physical; Adafruit_HUZZAH_ESP32_breakout_FIXED

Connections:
/3V3: JP1.1 (A), JP2.1 (A), JP3.1 (A), JP4.1 (A), JP5.1 (A), JP6.1 (A), JP7.1 (A), JP8.1 (A), JP9.1 (A), U1.14 (3V3)
/5V: J9.7, J9.8, J9.9, J17.1 (VBUS), J17.5 (VBUS), P7.1, P8.1, P9.1, PS2.VO, R46.1, U1.16 (VBAT)
/12V: J9.4, J9.5, J9.6, P4.1, P5.1, P6.1, PS2.VIN, R47.1; also elsewhere on the board
/72V: J9.1, J9.2, J9.3, P1.1, P2.1, P3.1, R48.1
/BRAKE: J9.16, R33.2, U1.18 (GPIO2)
/GND: D17.1 (K), D18.1 (K), D19.1 (K), J9.10, J9.11, J9.12, J9.13, J9.14, J9.15, J17.4 (GND), J17.8 (GND), J17.9 (Shield), J20.2, J20.4, J20.6, J20.8, J20.10, J20.12, J20.14, J20.16, JP1.3 (B), JP2.3 (B), JP3.3 (B), JP4.3 (B), JP5.3 (B), JP6.3 (B), JP7.3 (B), JP8.3 (B), JP9.3 (B), P10.1, P11.1, P12.1, P13.1, P14.1, PS2.GND, U1.15 (GND); also elsewhere on the board
/IN1: J20.15, R25.2, U1.26 (GPIO21)
/IN2: J20.13, R26.2, U1.25 (GPIO19)
/IN3: J20.11, R27.2, U1.24 (GPIO18)
/IN4: J20.9, R28.2, U1.23 (GPIO5)
/IN5: J20.7, R29.2, U1.22 (GPIO17)
/IN6: J20.5, R30.2, U1.21 (GPIO16)
/IN7: J20.3, R31.2, U1.20 (GPIO4)
/IN8: J20.1, R32.2, U1.19 (GPIO0)
/OUT1: U1.6 (GPIO32); also elsewhere on the board
/OUT2: U1.7 (GPIO33); also elsewhere on the board
/OUT3: U1.8 (GPIO25); also elsewhere on the board
/OUT4: U1.9 (GPIO26); also elsewhere on the board
/OUT5: U1.10 (GPIO27); also elsewhere on the board
/OUT6: U1.11 (GPIO14); also elsewhere on the board
/OUT7: U1.12 (GPIO12); also elsewhere on the board
/OUT8: U1.13 (GPIO13); also elsewhere on the board
unnamed: D17.2 (A), R46.2
unnamed: D18.2 (A), R47.2
unnamed: D19.2 (A), R48.2
unnamed: JP1.2 (C), R33.1
unnamed: JP2.2 (C), R25.1
unnamed: JP3.2 (C), R26.1
unnamed: JP4.2 (C), R27.1
unnamed: JP5.2 (C), R28.1
unnamed: JP6.2 (C), R29.1
unnamed: JP7.2 (C), R30.1
unnamed: JP8.2 (C), R31.1
unnamed: JP9.2 (C), R32.1

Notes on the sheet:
72V
GND
12V
NOTE : This block allows setting each input with pull up or pull down

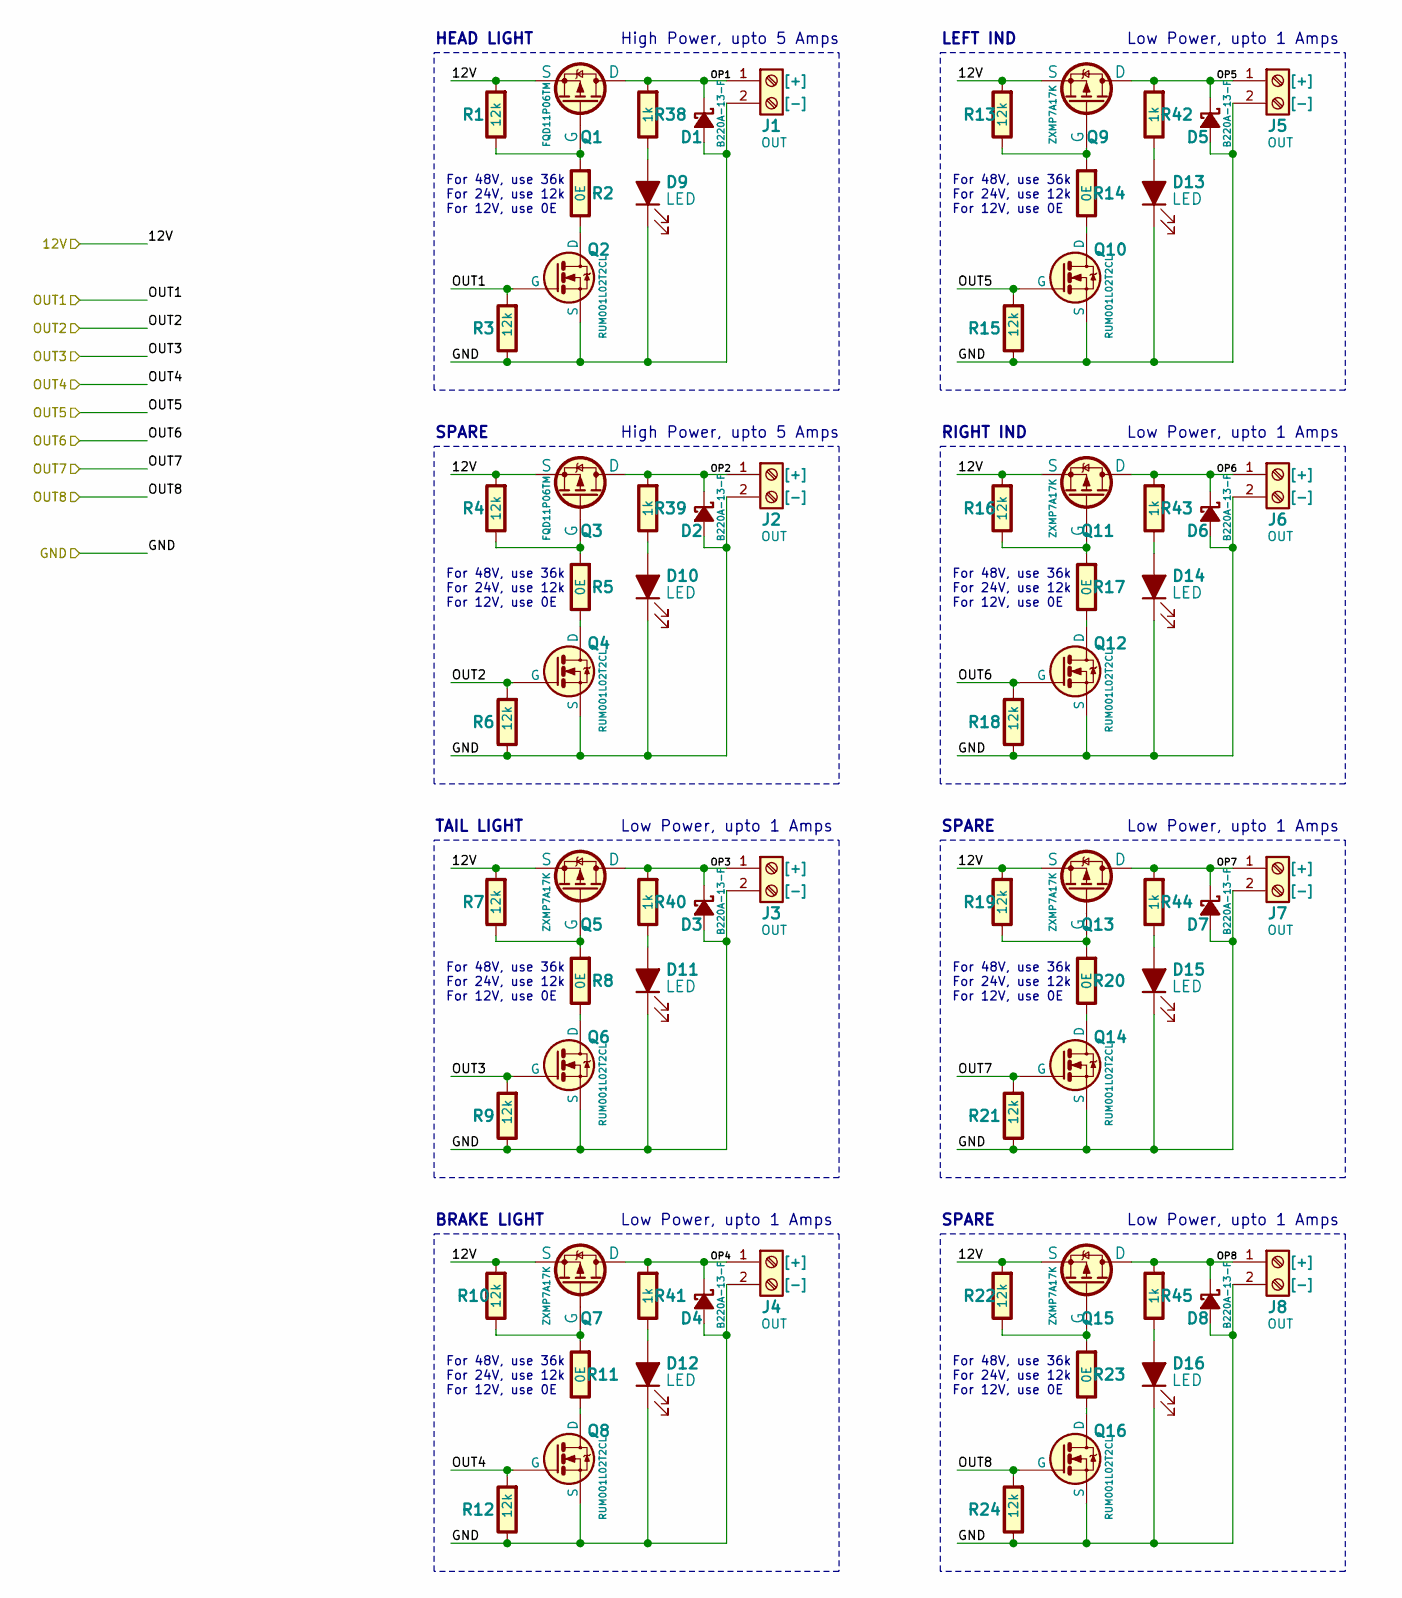
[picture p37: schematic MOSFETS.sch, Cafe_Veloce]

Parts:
D1, D2, D3, D4, D5, D6, D7, D8: B220A-13-F; D_SMA
D9, D10, D11, D12, D13, D14, D15, D16: LED; LED_0805_2012Metric
J1, J2, J3, J4, J5, J6, J7, J8: OUT; TerminalBlock_Wurth_1377-2_Horizontal
Q1, Q3: FQD11P06TM; TO-252-3_TabPin2
Q2, Q4, Q6, Q8, Q10, Q12, Q14, Q16: RUM001L02T2CL; SOT-723
Q5, Q7, Q9, Q11, Q13, Q15: ZXMP7A17K; TO-252-3_TabPin2
R1, R3, R4, R6, R7, R9, R10, R12, R13, R15, R16, R18, R19, R21, R22, R24: 12k; R_0805_2012Metric
R2, R5, R8, R11, R14, R17, R20, R23: 0E; R_0805_2012Metric
R38, R39, R40, R41, R42, R43, R44, R45: 1k; R_0805_2012Metric

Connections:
/12V: Q1.3 (S), Q3.3 (S), Q5.3 (S), Q7.3 (S), Q9.3 (S), Q11.3 (S), Q13.3 (S), Q15.3 (S), R1.2, R4.2, R7.2, R10.2, R13.2, R16.2, R19.2, R22.2; also elsewhere on the board
/GND: D1.2 (A), D2.2 (A), D3.2 (A), D4.2 (A), D5.2 (A), D6.2 (A), D7.2 (A), D8.2 (A), D9.1 (K), D10.1 (K), D11.1 (K), D12.1 (K), D13.1 (K), D14.1 (K), D15.1 (K), D16.1 (K), J1.2, J2.2, J3.2, J4.2, J5.2, J6.2, J7.2, J8.2, Q2.2 (S), Q4.2 (S), Q6.2 (S), Q8.2 (S), Q10.2 (S), Q12.2 (S), Q14.2 (S), Q16.2 (S), R3.1, R6.1, R9.1, R12.1, R15.1, R18.1, R21.1, R24.1; also elsewhere on the board
/MOSFETS/OP1: D1.1 (K), J1.1, Q1.2 (D), R38.2
/MOSFETS/OP2: D2.1 (K), J2.1, Q3.2 (D), R39.2
/MOSFETS/OP3: D3.1 (K), J3.1, Q5.2 (D), R40.2
/MOSFETS/OP4: D4.1 (K), J4.1, Q7.2 (D), R41.2
/MOSFETS/OP5: D5.1 (K), J5.1, Q9.2 (D), R42.2
/MOSFETS/OP6: D6.1 (K), J6.1, Q11.2 (D), R43.2
/MOSFETS/OP7: D7.1 (K), J7.1, Q13.2 (D), R44.2
/MOSFETS/OP8: D8.1 (K), J8.1, Q15.2 (D), R45.2
/OUT1: Q2.1 (G), R3.2; also elsewhere on the board
/OUT2: Q4.1 (G), R6.2; also elsewhere on the board
/OUT3: Q6.1 (G), R9.2; also elsewhere on the board
/OUT4: Q8.1 (G), R12.2; also elsewhere on the board
/OUT5: Q10.1 (G), R15.2; also elsewhere on the board
/OUT6: Q12.1 (G), R18.2; also elsewhere on the board
/OUT7: Q14.1 (G), R21.2; also elsewhere on the board
/OUT8: Q16.1 (G), R24.2; also elsewhere on the board
unnamed: D9.2 (A), R38.1
unnamed: D10.2 (A), R39.1
unnamed: D11.2 (A), R40.1
unnamed: D12.2 (A), R41.1
unnamed: D13.2 (A), R42.1
unnamed: D14.2 (A), R43.1
unnamed: D15.2 (A), R44.1
unnamed: D16.2 (A), R45.1
unnamed: Q1.1 (G), R1.1, R2.2
unnamed: Q2.3 (D), R2.1
unnamed: Q3.1 (G), R4.1, R5.2
unnamed: Q4.3 (D), R5.1
unnamed: Q5.1 (G), R7.1, R8.2
unnamed: Q6.3 (D), R8.1
unnamed: Q7.1 (G), R10.1, R11.2
unnamed: Q8.3 (D), R11.1
unnamed: Q9.1 (G), R13.1, R14.2
unnamed: Q10.3 (D), R14.1
unnamed: Q11.1 (G), R16.1, R17.2
unnamed: Q12.3 (D), R17.1
unnamed: Q13.1 (G), R19.1, R20.2
unnamed: Q14.3 (D), R20.1
unnamed: Q15.1 (G), R22.1, R23.2
unnamed: Q16.3 (D), R23.1

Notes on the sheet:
High Power, upto 5 Amps
HEAD LIGHT
TAIL LIGHT
LEFT IND
For 48V, use 36k For 24V, use 12k For 12V, use 0E
SPARE
Low Power, upto 1 Amps
BRAKE LIGHT
RIGHT IND

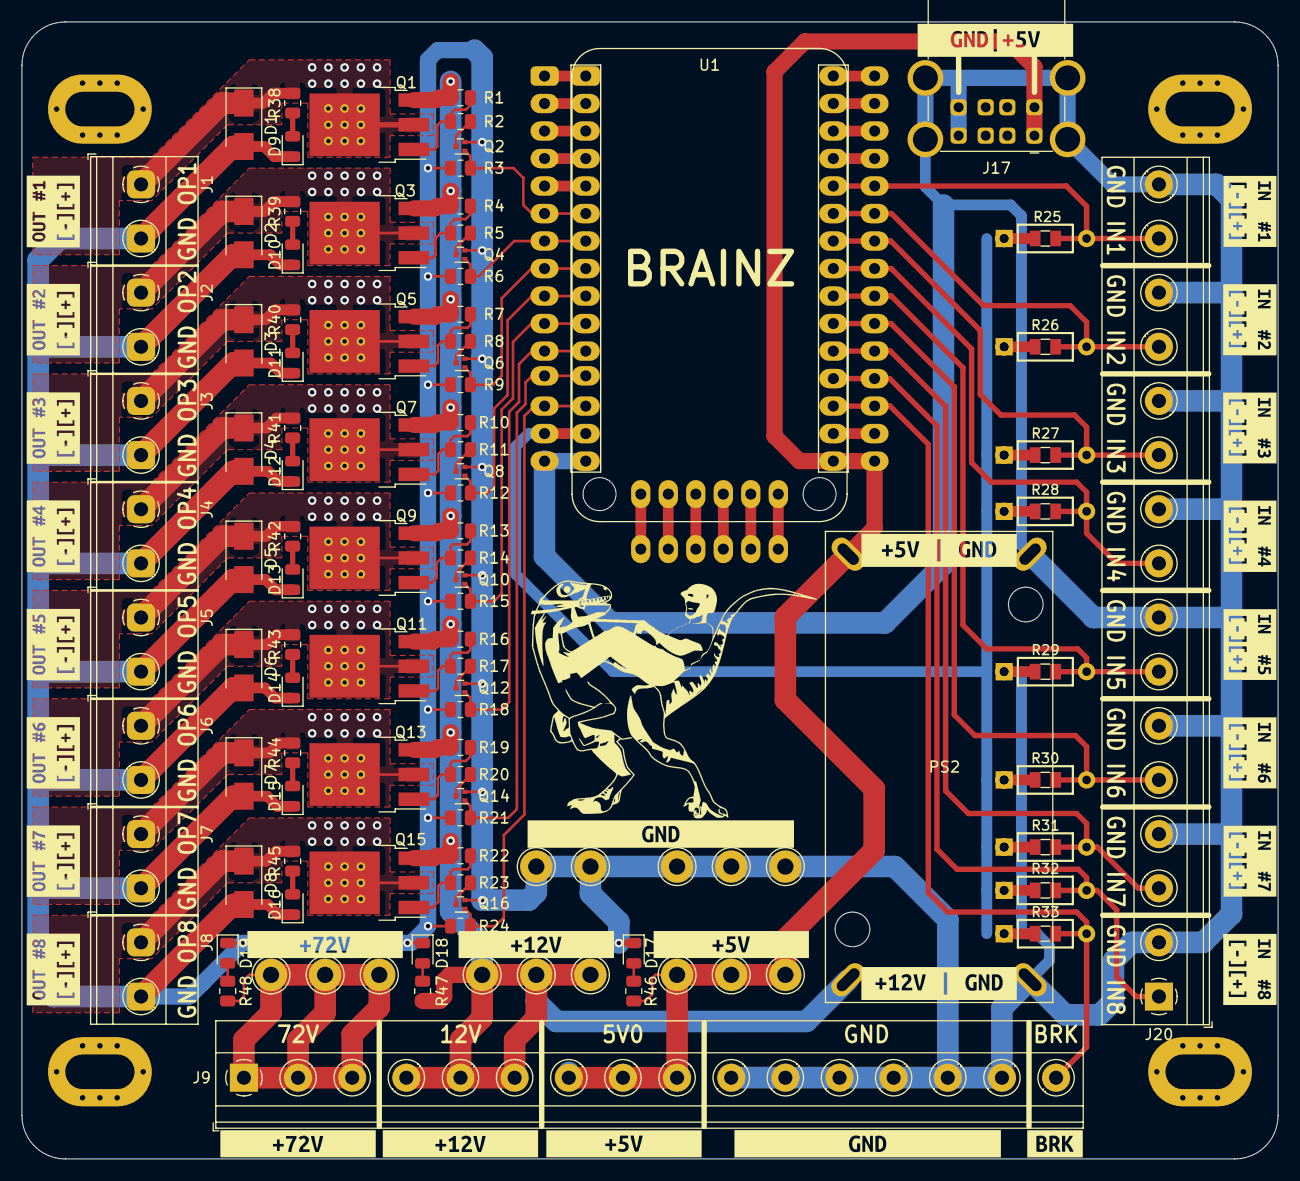
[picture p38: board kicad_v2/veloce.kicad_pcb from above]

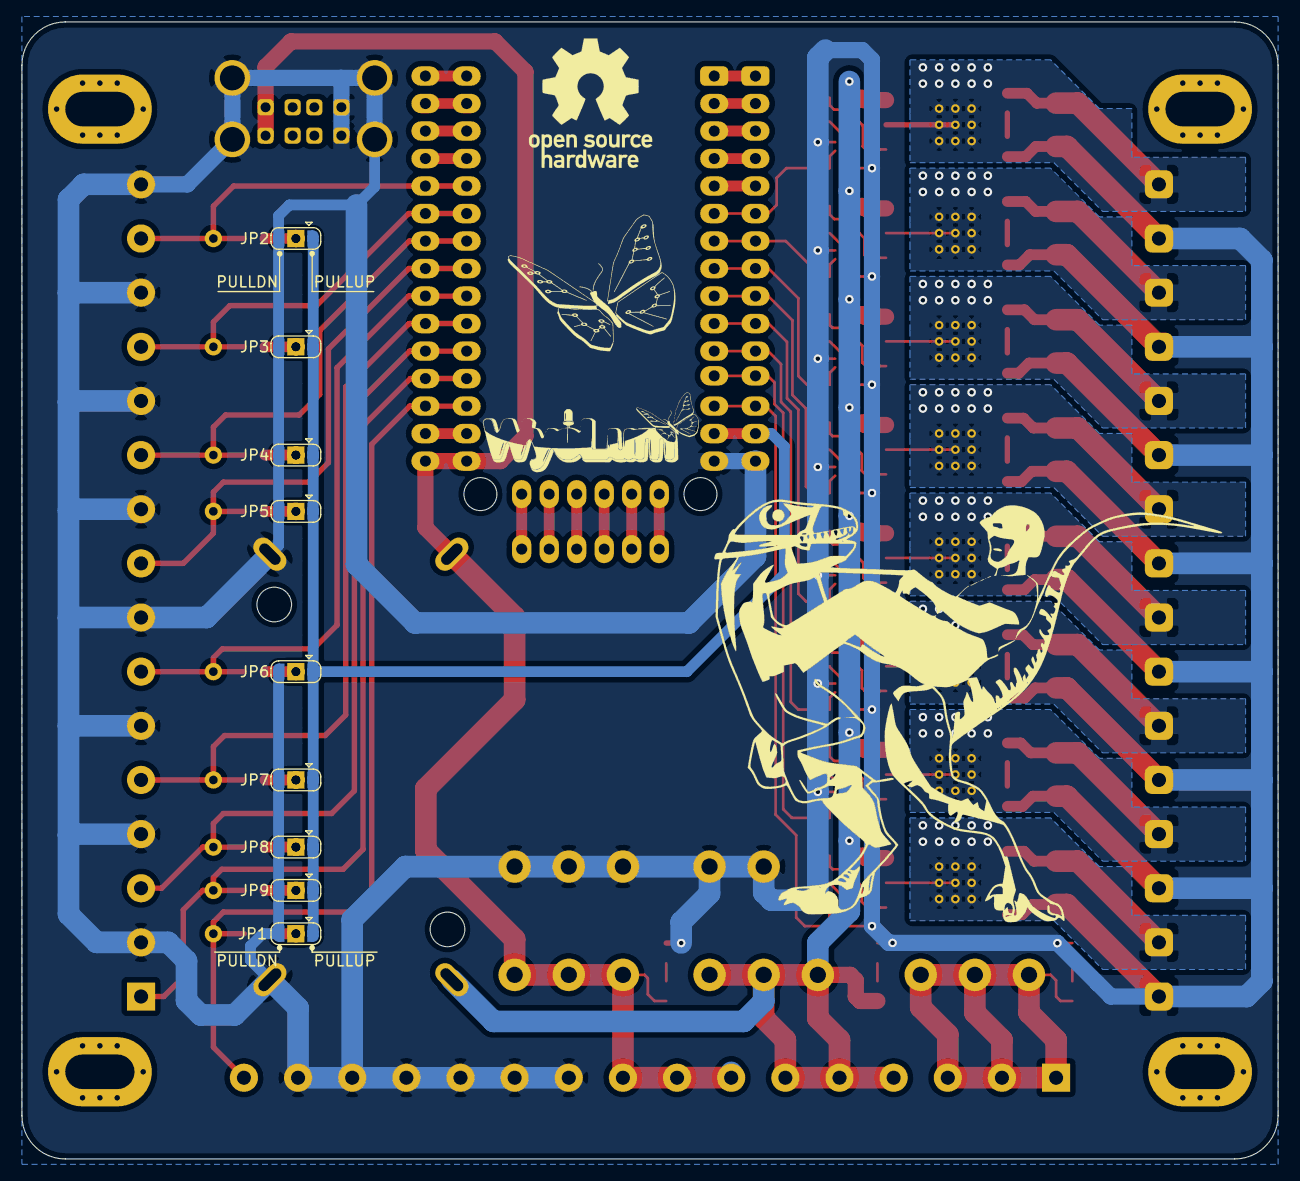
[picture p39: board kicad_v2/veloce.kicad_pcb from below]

Board: 2 copper layers, 116.0 x 105.0 mm, 156 parts (16 on the bottom side), 66 nets.

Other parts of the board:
kibuzzard-61BB7D75: G***; label_brk
kibuzzard-61BB7E28, kibuzzard-614E1DC4: G***; label_12V
kibuzzard-61BB7E88, kibuzzard-614E1DE5: G***; label_72V
kibuzzard-61BC3C7D: G***; label_buck_output
kibuzzard-61BC3C42: G***; label_buck_input
kibuzzard-61BC84E3: G***; label_5V_USB
kibuzzard-61BC4209, kibuzzard-61BC4209#2: G***; label_GND
kibuzzard-614E1E36, kibuzzard-614E1E36#2: G***; label_5V
kibuzzard-614E18A2: G***; label_OUT5
kibuzzard-614E18AA: G***; label_OUT6
kibuzzard-614E18B2: G***; label_OUT7
kibuzzard-614E18BA: G***; label_OUT8
kibuzzard-614E19A5: G***; label_IN2
kibuzzard-614E19AF: G***; label_IN3
kibuzzard-614E19B6: G***; label_IN4
kibuzzard-614E19C0: G***; label_IN5
kibuzzard-614E19C8: G***; label_IN6
kibuzzard-614E19D4: G***; label_IN7
kibuzzard-614E19DD: G***; label_IN8
kibuzzard-614E188E: G***; label_OUT3
kibuzzard-614E196C: G***; label_IN1
kibuzzard-614E1815: G***; label_OUT1
kibuzzard-614E1883: G***; label_OUT2
kibuzzard-614E1899: G***; label_OUT4

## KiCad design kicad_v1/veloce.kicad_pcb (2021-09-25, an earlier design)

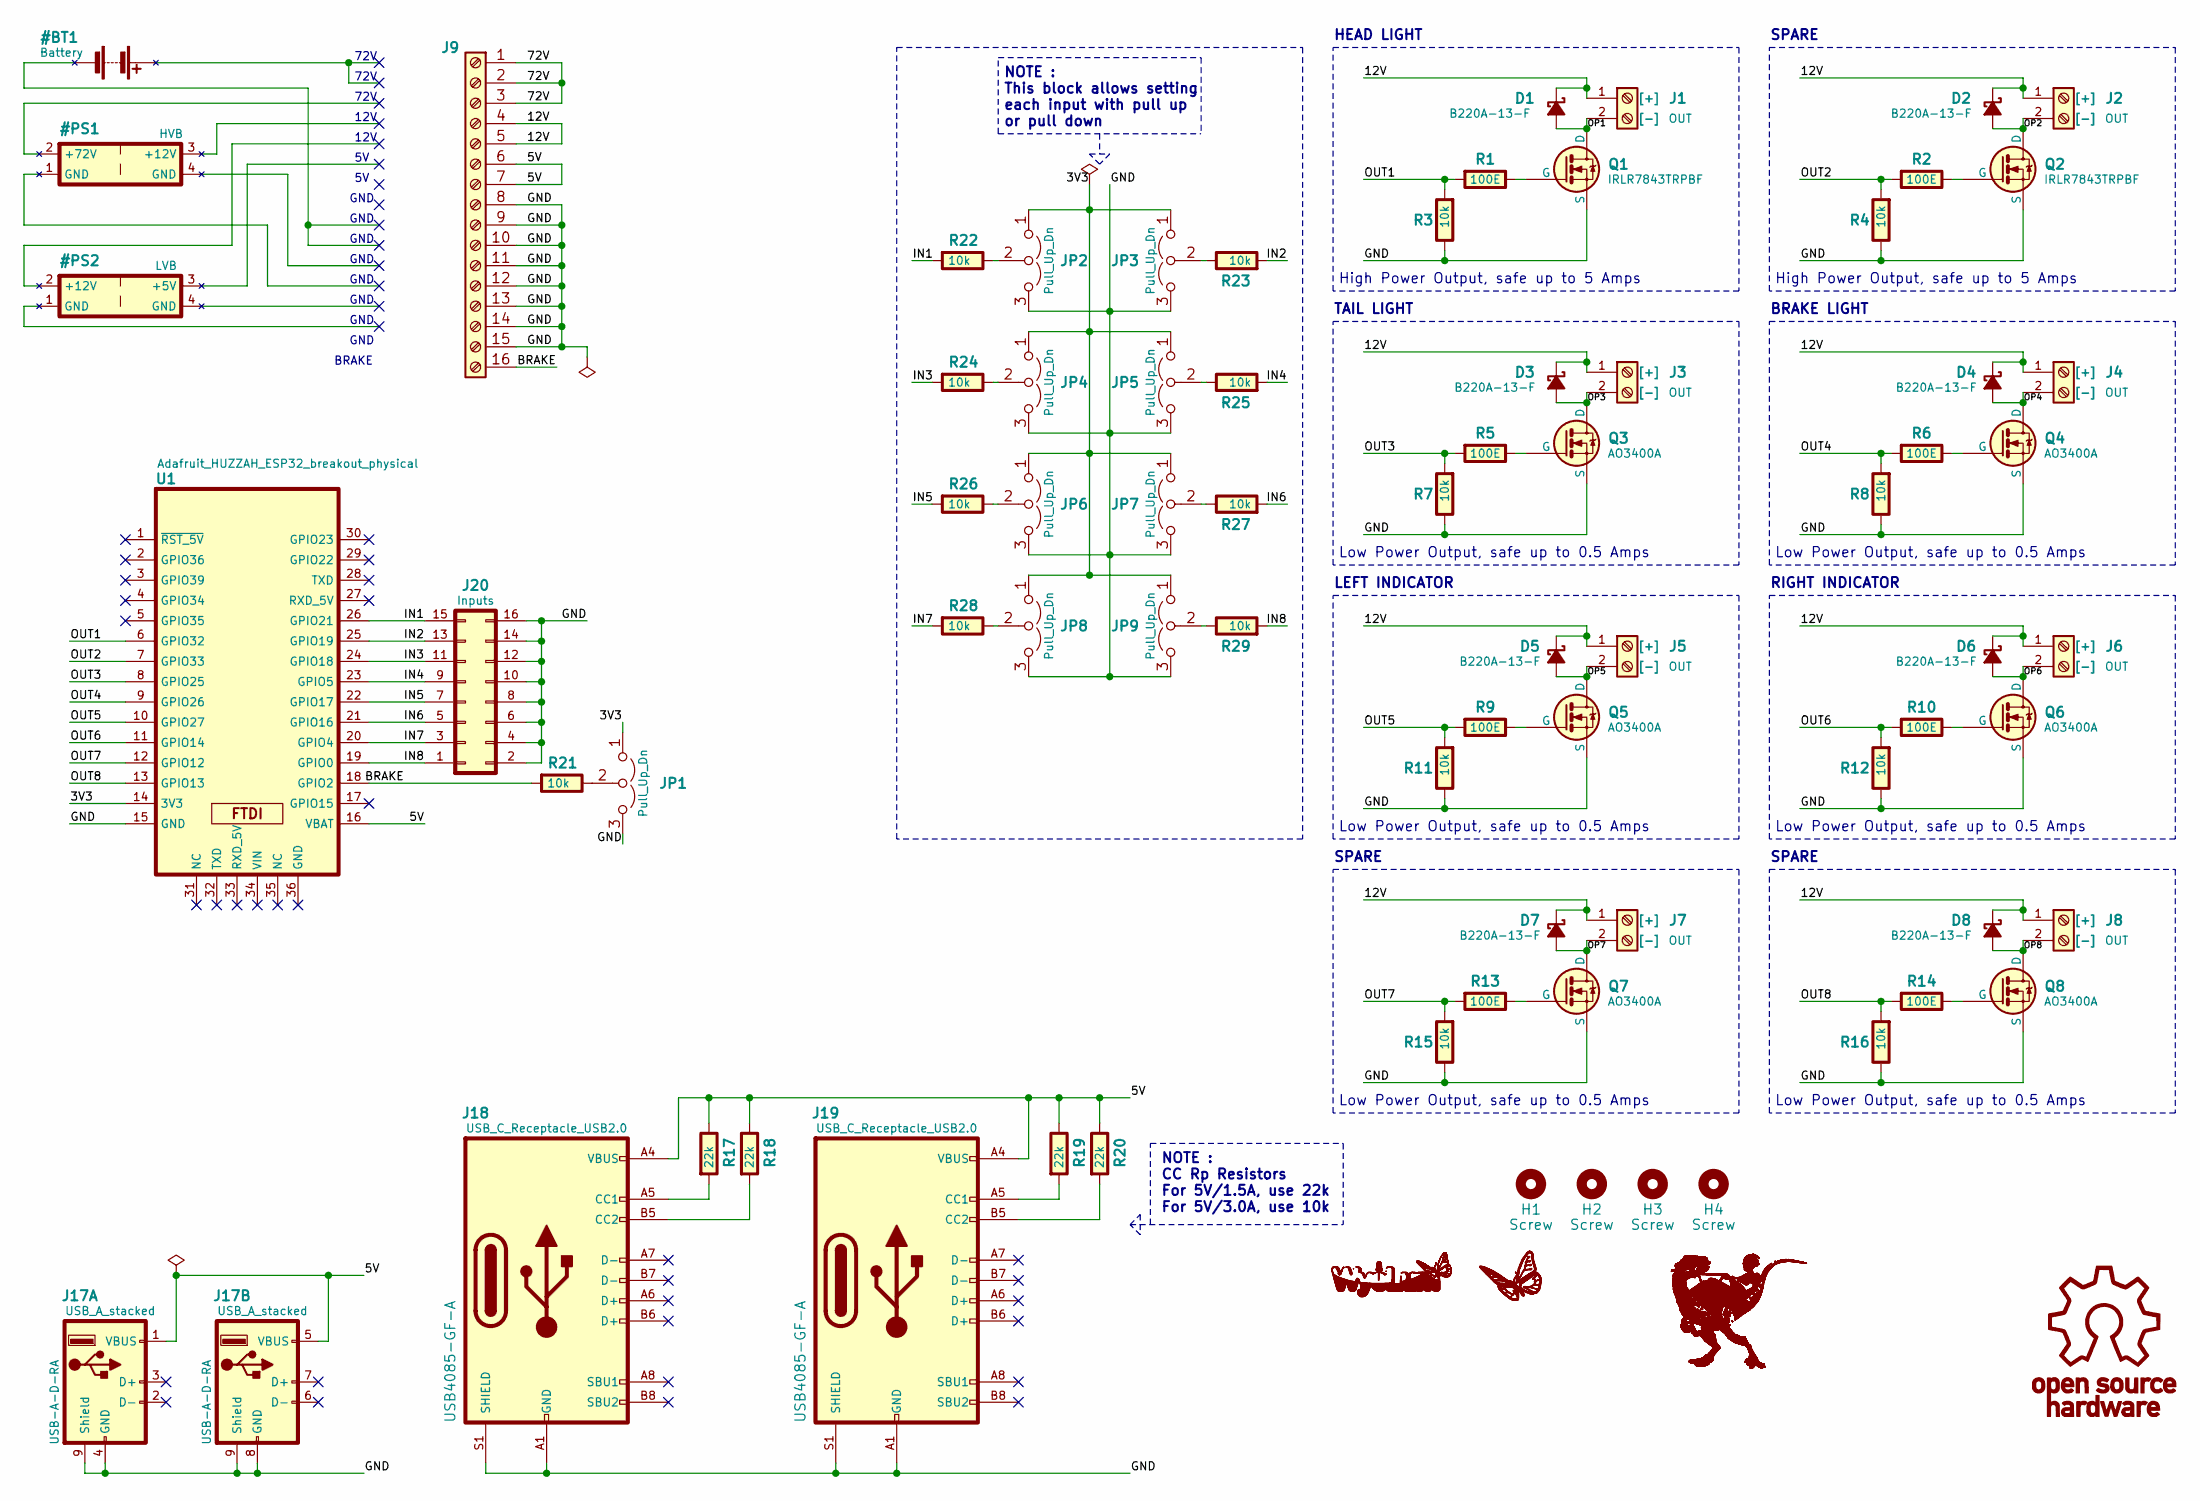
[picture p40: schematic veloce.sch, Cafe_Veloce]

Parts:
D1, D2, D3, D4, D5, D6, D7, D8: B220A-13-F; D_SMB
G1: Logo_Veloce; VR_logo4
G2: Logo_Veloce; VR_logo5
G3: Logo_Veloce; VR_logo2
G4: Logo_Veloce; VR_logo3
G5: LOGO_WL; logo_butterfly_silk_15x12
G6: LOGO_WL; logo_butterfly_mask_15x12
G7: Logo_OSHW; Logo_OSHW-11.4x12mm_SilkScreen
G8: Logo_Wyolum; logo_wyolum_silk_20x8
G9: Logo_Wyolum; logo_wyolum_mask_20x8
H1, H2, H3, H4: Screw; MountingHole_3.2mm_M3_Pad_Via
J1, J2, J3, J4, J5, J6, J7, J8: OUT; TerminalBlock_Wurth_1377-2_Horizontal
J9: PWR; TerminalBlock_Wurth_1377-16_Horizontal
J17: USB_A_stacked; USB_A_Wuerth_61400826021_Horizontal_Stacked
J18, J19: USB_C_Receptacle_USB2.0; USB_C_GCT_USB4085-GF-A_REVA
J20: Inputs; TerminalBlock_Wurth_1377-16_Horizontal
JP1, JP2, JP3, JP4, JP5, JP6, JP7, JP8, JP9: Pull_Up_Dn; SolderJumper-3_P1.3mm_Open_RoundedPad1.0x1.5mm_THT
Q1, Q2: IRLR7843TRPBF; MOSFET_D_PAK
Q3, Q4, Q5, Q6, Q7, Q8: AO3400A; SOT-23
R1, R2, R5, R6, R9, R10, R13, R14: 100E; R_0805_2012Metric
R3, R4, R7, R8, R11, R12, R15, R16: 10k; R_0805_2012Metric
R17, R18, R19, R20: 22k; r_0805_THT
R21, R22, R23, R24, R25, R26, R27, R28, R29: 10k; r_0805_THT
U1: Adafruit_HUZZAH_ESP32_breakout_physical; Adafruit_HUZZAH_ESP32_breakout_sparepads

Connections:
/3V3: JP1.1 (A), JP2.1 (A), JP3.1 (A), JP4.1 (A), JP5.1 (A), JP6.1 (A), JP7.1 (A), JP8.1 (A), JP9.1 (A), U1.14 (3V3)
/5V: J9.6, J9.7, J17.1 (VBUS), J17.5 (VBUS), J18.A4 (VBUS), J18.A9 (VBUS), J18.B4 (VBUS), J18.B9 (VBUS), J19.A4 (VBUS), J19.A9 (VBUS), J19.B4 (VBUS), J19.B9 (VBUS), R17.1, R18.1, R19.1, R20.1, U1.16 (VBAT)
/12V: D1.1 (K), D2.1 (K), D3.1 (K), D4.1 (K), D5.1 (K), D6.1 (K), D7.1 (K), D8.1 (K), J1.1, J2.1, J3.1, J4.1, J5.1, J6.1, J7.1, J8.1, J9.4, J9.5
/72V: J9.1, J9.2, J9.3
/BRAKE: J9.16, R21.2, U1.18 (GPIO2)
/GND: J9.8, J9.9, J9.10, J9.11, J9.12, J9.13, J9.14, J9.15, J17.4 (GND), J17.8 (GND), J17.9 (Shield), J18.A1 (GND), J18.A12 (GND), J18.B1 (GND), J18.B12 (GND), J18.S1 (SHIELD), J19.A1 (GND), J19.A12 (GND), J19.B1 (GND), J19.B12 (GND), J19.S1 (SHIELD), J20.2, J20.4, J20.6, J20.8, J20.10, J20.12, J20.14, J20.16, JP1.3 (B), JP2.3 (B), JP3.3 (B), JP4.3 (B), JP5.3 (B), JP6.3 (B), JP7.3 (B), JP8.3 (B), JP9.3 (B), Q1.2 (S), Q2.2 (S), Q3.2 (S), Q4.2 (S), Q5.2 (S), Q6.2 (S), Q7.2 (S), Q8.2 (S), R3.1, R4.1, R7.1, R8.1, R11.1, R12.1, R15.1, R16.1, U1.15 (GND)
/IN1: J20.15, R22.2, U1.26 (GPIO21)
/IN2: J20.13, R23.2, U1.25 (GPIO19)
/IN3: J20.11, R24.2, U1.24 (GPIO18)
/IN4: J20.9, R25.2, U1.23 (GPIO5)
/IN5: J20.7, R26.2, U1.22 (GPIO17)
/IN6: J20.5, R27.2, U1.21 (GPIO16)
/IN7: J20.3, R28.2, U1.20 (GPIO4)
/IN8: J20.1, R29.2, U1.19 (GPIO0)
/OP1: D1.2 (A), J1.2, Q1.3 (D)
/OP2: D2.2 (A), J2.2, Q2.3 (D)
/OP3: D3.2 (A), J3.2, Q3.3 (D)
/OP4: D4.2 (A), J4.2, Q4.3 (D)
/OP5: D5.2 (A), J5.2, Q5.3 (D)
/OP6: D6.2 (A), J6.2, Q6.3 (D)
/OP7: D7.2 (A), J7.2, Q7.3 (D)
/OP8: D8.2 (A), J8.2, Q8.3 (D)
/OUT1: R1.2, R3.2, U1.6 (GPIO32)
/OUT2: R2.2, R4.2, U1.7 (GPIO33)
/OUT3: R5.2, R7.2, U1.8 (GPIO25)
/OUT4: R6.2, R8.2, U1.9 (GPIO26)
/OUT5: R9.2, R11.2, U1.10 (GPIO27)
/OUT6: R10.2, R12.2, U1.11 (GPIO14)
/OUT7: R13.2, R15.2, U1.12 (GPIO12)
/OUT8: R14.2, R16.2, U1.13 (GPIO13)
unnamed: J18.A5 (CC1), R17.2
unnamed: J18.B5 (CC2), R18.2
unnamed: J19.A5 (CC1), R19.2
unnamed: J19.B5 (CC2), R20.2
unnamed: JP1.2 (C), R21.1
unnamed: JP2.2 (C), R22.1
unnamed: JP3.2 (C), R23.1
unnamed: JP4.2 (C), R24.1
unnamed: JP5.2 (C), R25.1
unnamed: JP6.2 (C), R26.1
unnamed: JP7.2 (C), R27.1
unnamed: JP8.2 (C), R28.1
unnamed: JP9.2 (C), R29.1
unnamed: Q1.1 (G), R1.1
unnamed: Q2.1 (G), R2.1
unnamed: Q3.1 (G), R5.1
unnamed: Q4.1 (G), R6.1
unnamed: Q5.1 (G), R9.1
unnamed: Q6.1 (G), R10.1
unnamed: Q7.1 (G), R13.1
unnamed: Q8.1 (G), R14.1

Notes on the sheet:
High Power Output, safe up to 5 Amps
Low Power Output, safe up to 0.5 Amps
NOTE : CC Rp Resistors For 5V/1.5A, use 22k For 5V/3.0A, use 10k
HEAD LIGHT
SPARE
TAIL LIGHT
BRAKE LIGHT
LEFT INDICATOR
RIGHT INDICATOR
72V
GND
12V
NOTE : This block allows setting each input with pull up or pull down
BRAKE

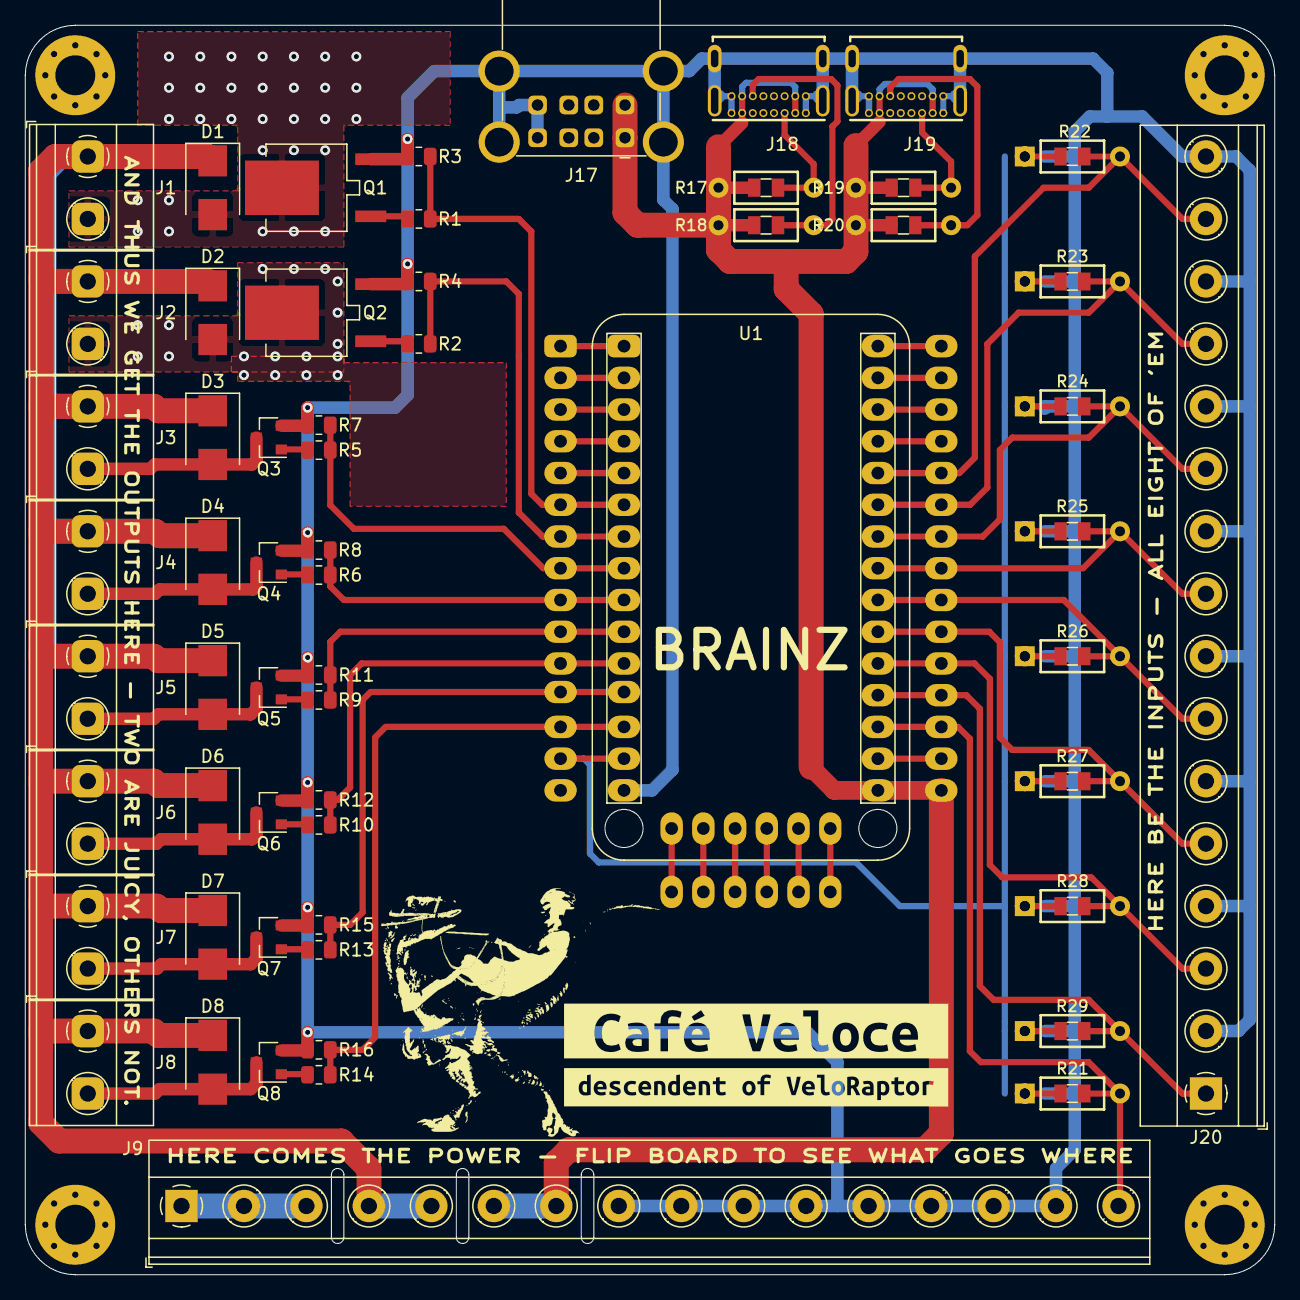
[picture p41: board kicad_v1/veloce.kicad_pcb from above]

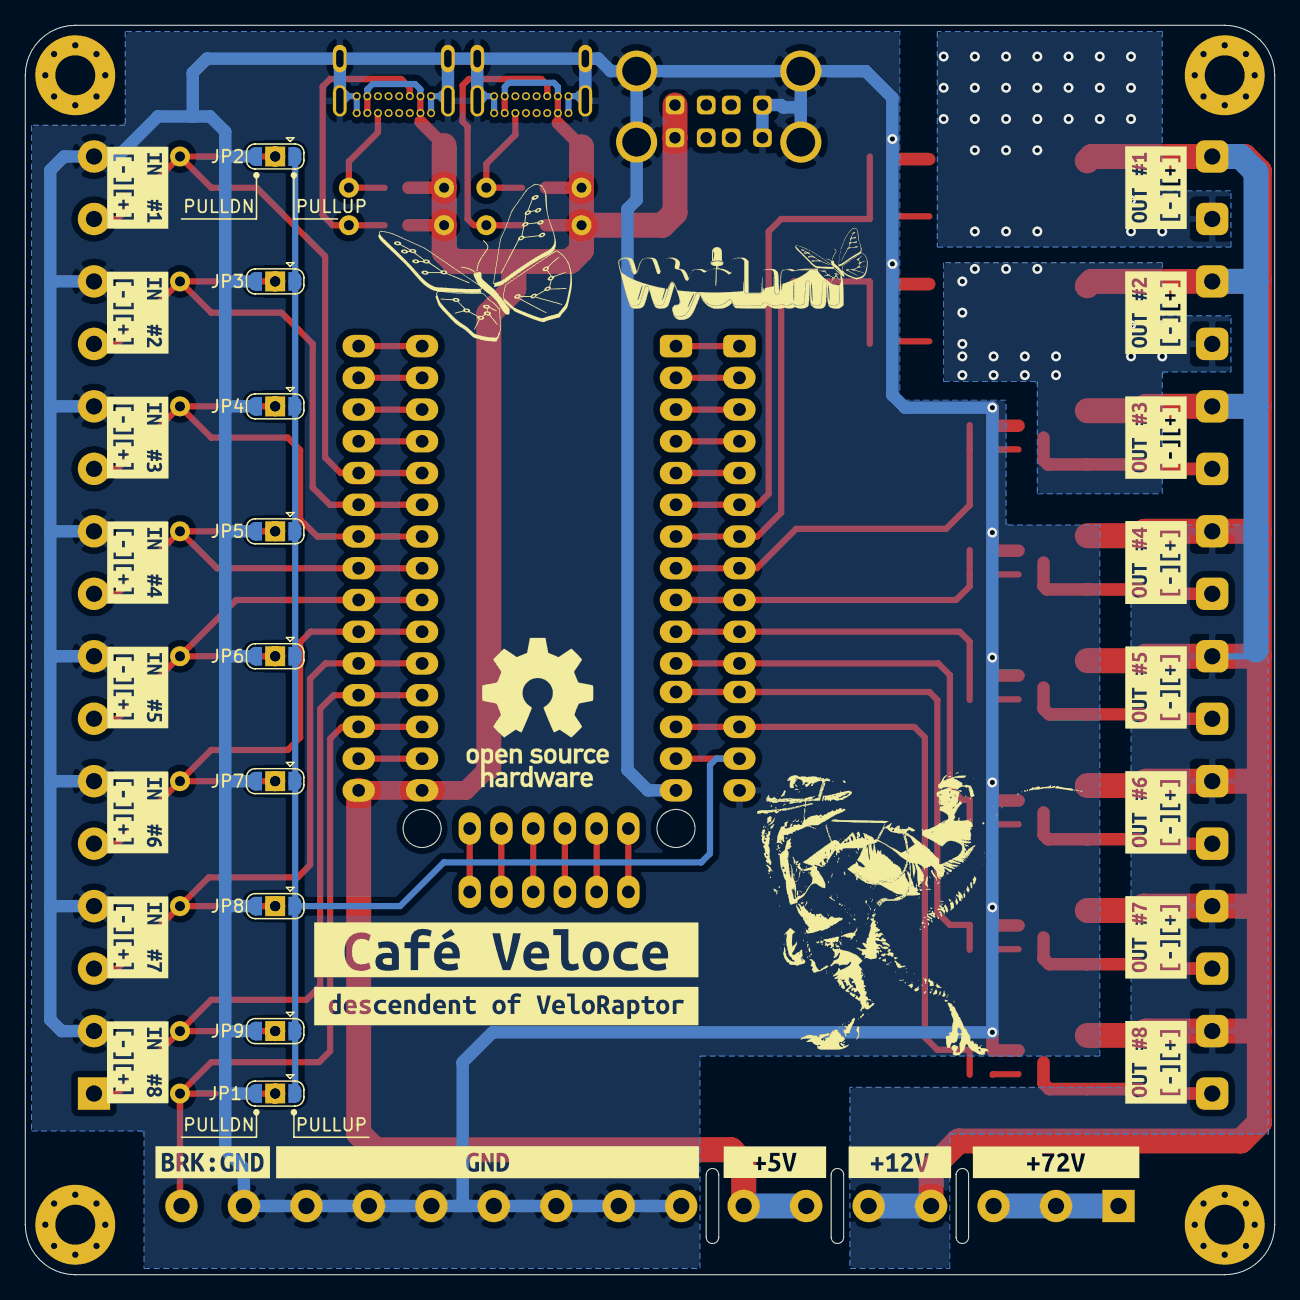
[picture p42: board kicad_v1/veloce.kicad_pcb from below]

Board: 2 copper layers, 100.0 x 100.0 mm, 106 parts (39 on the bottom side), 51 nets.

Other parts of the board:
kibuzzard-614E1BE6: #G3; label_Cafe_Veloce
kibuzzard-614E1BE6#2: #G1; label_Cafe_Veloce
kibuzzard-614E1CD8: #G4; label_VeloRaptor
kibuzzard-614E1CD8#2: #G2; label_VeloRaptor
kibuzzard-614E1DC4: #G6; label_12V
kibuzzard-614E1DE5: #G5; label_72V
kibuzzard-614E1E6D: #G8; label_GND
kibuzzard-614E1E9D: #G9; label_Brake
kibuzzard-614E1E36: #G7; label_5V
kibuzzard-614E18A2: #G14; label_OUT5
kibuzzard-614E18AA: #G15; label_OUT6
kibuzzard-614E18B2: #G16; label_OUT7
kibuzzard-614E18BA: #G17; label_OUT8
kibuzzard-614E19A5: #G19; label_IN2
kibuzzard-614E19AF: #G20; label_IN3
kibuzzard-614E19B6: #G21; label_IN4
kibuzzard-614E19C0: #G22; label_IN5
kibuzzard-614E19C8: #G23; label_IN6
kibuzzard-614E19D4: #G24; label_IN7
kibuzzard-614E19DD: #G25; label_IN8
kibuzzard-614E188E: #G12; label_OUT3
kibuzzard-614E196C: #G18; label_IN1
kibuzzard-614E1815: #G10; label_OUT1
kibuzzard-614E1883: #G11; label_OUT2
kibuzzard-614E1899: #G13; label_OUT4

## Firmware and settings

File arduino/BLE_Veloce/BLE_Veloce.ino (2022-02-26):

/*
    Based on Neil Kolban example for IDF: https://github.com/nkolban/esp32-snippets/blob/master/cpp_utils/tests/BLE%20Tests/SampleWrite.cpp
    Ported to Arduino ESP32 by Evandro Copercini
*/

#include <BLEDevice.h>
#include <BLEUtils.h>
#include <BLEServer.h>
#include <Veloce.h>

bool status[N_OUT];
/*
message:
8 bytes
0 lights
1 left
2 right
3 brake
4 horn
5 reserved
6 reserved
7 reserved
*/

// See the following for generating UUIDs:
// https://www.uuidgenerator.net/

#define             SERVICE_UUID "77dcdaf7-4003-4497-b52d-7c7f6b82d2a5"
#define PULL_CHARACTERISTIC_UUID "9ce9bc50-bed6-43a7-a0de-468eed0d2776"
#define PUSH_CHARACTERISTIC_UUID "133beef8-d5c6-43ed-8aa6-e4366d1bb523"
bool LightState = false;
#define LIGHTPIN OUT_1

BLECharacteristic VeloceLightsPushCharacteristic
(
 PUSH_CHARACTERISTIC_UUID,
 BLECharacteristic::PROPERTY_NOTIFY |
 BLECharacteristic::PROPERTY_READ |
 BLECharacteristic::PROPERTY_WRITE
 );

BLEDescriptor VeloceLightsPushDescriptor(PUSH_CHARACTERISTIC_UUID);

bool deviceConnected = false;

class MyCallbacks: public BLECharacteristicCallbacks {
    void onWrite(BLECharacteristic *pCharacteristic) {
      std::string value = pCharacteristic->getValue();
      if (value.length() > 0) {
        Serial.print("New value: ");
        for (int i = 0; i < value.length(); i++){
          Serial.print(value[i]);
	}
        Serial.println();
        if (value[0] == '1'){
          LightState = true;
	}
        else if(value[0] == '0'){
          LightState = false;
	}
        digitalWrite(LIGHTPIN,LightState);
      }
    }
    
    void onRead(BLECharacteristic* pCharacteristic){
      Serial.println("onRead()");
      char msg[N_OUT + 1] = "00000000";
      for(int i = 0; i < N_OUT; i++){
	if(status[i]){
	  msg[i] = '1';
	}
	else{
	  msg[i] = '0';
	}
      }
      pCharacteristic->setValue(msg);
    }
};
class MyServerCallbacks: public BLEServerCallbacks {
    void onConnect(BLEServer* pServer) {
      Serial.println("connected");
      deviceConnected = true;
    };

    void onDisconnect(BLEServer* pServer) {
      Serial.println("disconnected");
      deviceConnected = false;
    }
};

void setup() {
  Serial.begin(115200);
  Serial.println("Cafe Veloce");
  Serial.print("       SERVICE_UUID:");
  Serial.println(SERVICE_UUID);
  Serial.print("PULL_CHARACTERISTIC_UUID:");
  Serial.println(PULL_CHARACTERISTIC_UUID);
  Serial.print("PUSH_CHARACTERISTIC_UUID:");
  Serial.println(PUSH_CHARACTERISTIC_UUID);

  for (int i = 0; i < N_OUT; i++){
    pinMode(OUT_PINS[i],OUTPUT);
    pinMode(IN_PINS[i],INPUT_PULLUP);

    status[i] = digitalRead(IN_PINS[i]);
    digitalWrite(OUT_PINS[i], !status[i]);
  }

  for (int i = 0; i < N_IN; i++){
  }

  BLEDevice::init("Cafe Veloce");
  BLEServer *pServer = BLEDevice::createServer();

  BLEService *pService = pServer->createService(SERVICE_UUID);

  BLECharacteristic *pCharacteristic = pService->createCharacteristic(
                                         PULL_CHARACTERISTIC_UUID,
                                         BLECharacteristic::PROPERTY_READ |
                                         BLECharacteristic::PROPERTY_WRITE
                                       );
  pService->addCharacteristic(&VeloceLightsPushCharacteristic);
  VeloceLightsPushDescriptor.setValue("Veloce Light Status");
  VeloceLightsPushCharacteristic.addDescriptor(&VeloceLightsPushDescriptor);

  pCharacteristic->setCallbacks(new MyCallbacks());
  pServer->setCallbacks(new MyServerCallbacks());
  pCharacteristic->setValue("0");
  pService->start();

  BLEAdvertising *pAdvertising = pServer->getAdvertising();
  pAdvertising->start();
}

void loop() {
  bool status_changed = false;
  
  for(int i=0; i < N_OUT; i++){
    bool val = digitalRead(IN_PINS[i]);
    if(status[i] != val){
      status[i] = val;
      status_changed = true;
      digitalWrite(OUT_PINS[i], val);
    }
  }
  if(status_changed){
    update_ble_client();
  }
}

void update_ble_client(){
  char *msg = "00000000";
  for(int i = 0; i < N_OUT; i++){
    if(status[i]){
      msg[i] = '1';
    }
  }
  if(deviceConnected){
    VeloceLightsPushCharacteristic.setValue(msg);
    VeloceLightsPushCharacteristic.notify();
  }
  Serial.println(msg);
}

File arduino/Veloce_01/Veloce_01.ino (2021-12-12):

//#define ESP8266
#include <Veloce.h>

bool last_light_sw_state;
bool last_brake_sw_state;

bool last_brake_state;
void setup() {
  delay(500);
  pinMode(RIGHT_IN, INPUT_PULLUP);
  pinMode(LEFT_IN, INPUT_PULLUP);
  pinMode(BRAKE_IN, INPUT_PULLUP);


  pinMode(LIGHTS_OUT, OUTPUT);
  pinMode(LEFT_OUT, OUTPUT);
  pinMode(RIGHT_OUT, OUTPUT);
  pinMode(BRAKE_OUT, OUTPUT);

#ifndef ESP8266
  pinMode(HORN_IN, INPUT_PULLUP);
  pinMode(HORN_OUT, OUTPUT);
#endif
  
  pinMode(13, OUTPUT);
  Serial.begin(115200);

  digitalWrite(LIGHTS_OUT, HIGH);
  last_brake_state = !digitalRead(BRAKE_IN);
  Serial.println("Cafe Veloce version 01");
}
int horn_count = 0;
void update_horn(){
#ifndef ESP8266
  bool horn = !digitalRead(HORN_IN);
  horn_count += horn;
  
  if(horn){
    if(horn_count > 1){
      digitalWrite(HORN_OUT, horn);
    }
  }
  else{
    horn_count = 0;
    digitalWrite(HORN_OUT, false);
  }
#endif
}

void loop(){
  digitalWrite(LEFT_OUT, !digitalRead(LEFT_IN));
  digitalWrite(RIGHT_OUT, !digitalRead(RIGHT_IN));
  update_brake();
  update_horn();
}
void update_brake(){
  bool brake_state = !digitalRead(BRAKE_IN);
  if(brake_state && !last_brake_state){
    for(int i=0; i<2 && !digitalRead(BRAKE_IN); i++){
      digitalWrite(BRAKE_OUT, HIGH);
      delay(50);
      digitalWrite(BRAKE_OUT, LOW);
      delay(50);
    }
  }
  last_brake_state = brake_state;
  if(last_brake_state){
    digitalWrite(BRAKE_OUT, HIGH);
  }
  else{
    digitalWrite(BRAKE_OUT, millis() % 5 == 0);
  }
}

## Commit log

2021-09-23 prototype gerber ready
    [Sample-BOM_JLCSMT.xlsx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]
2021-09-23 added superawesome logos
    [veloce.kicad_pcb, veloce.sch, veloce_BOM_JLCSMT.xlsx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]
2021-09-24 added labels and right angle connector 3D models
    [CUI_DEVICES_TB002V-500-P02GR.step, CUI_DEVICES_TB002V-500-P16GR.step, Conn_Wurth_RA_02.step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]
2021-09-25 JLCpcb production files ready
    [veloce-B_Cu.gbr, veloce-B_Mask.gbr, veloce-B_Paste.gbr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]
2021-11-06 added design files prior to first ride
    [cable_guide_0.dxf, cable_guide_0.scad]
2021-11-14 more frame design
    [kickstand_plate.scad]
2021-12-12 Initital arduino code commit
    [drillpress_spacer.scad]
2021-12-16 CV rev2 PCB
    [CUI_DEVICES_TB002V-500-P02GR.step, CUI_DEVICES_TB002V-500-P16GR.step, CUI_DEVICES_UJ2-ADH-W1-TH.step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]
2021-12-21 JLCpcb production files ready for CV rev 2
    [MOSFETS.sch, Sample_BOM_PCBWay.xlsx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]
2022-01-05 add BLE light sample
2022-02-26 debugging BLE stuff and board resetting
    [BLE_Veloce.ino]
2022-02-26 Updated Veloce.h
    [cable_guide_0.scad]
2022-02-26 added Veloce_02.ino. No BLE
2023-09-23 added sepearate line for pulsed brake light

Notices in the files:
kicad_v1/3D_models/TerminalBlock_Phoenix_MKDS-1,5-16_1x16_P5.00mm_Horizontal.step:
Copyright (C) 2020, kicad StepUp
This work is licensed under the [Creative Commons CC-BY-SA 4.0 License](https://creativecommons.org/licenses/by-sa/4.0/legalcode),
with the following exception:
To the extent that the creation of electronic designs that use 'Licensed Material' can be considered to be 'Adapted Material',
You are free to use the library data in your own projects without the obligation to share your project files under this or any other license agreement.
